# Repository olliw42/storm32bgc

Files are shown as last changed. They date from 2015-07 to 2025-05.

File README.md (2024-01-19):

STorM32 BGC
===========

<strong>STM32 32-bit microcontroller based 3-axis brushless gimbal controller board</strong>

scheme and design by OlliW (except of STorM32 v4.1)<br>
v0.17: layout by Martinez and OlliW<br>
v4.1: design by KrattWorks

latest board version: v3.3, v4.1

the STorM32 BGC boards and all other hardware published here are open source hardware, under the terms of the TAPR Open Hardware License as published by the Free Hardware Foundation, see http://www.tapr.org/ohl.html

the firmwares are free and the GUI is open source, for the details of the terms of usage/licenses see <a href="http://www.olliw.eu/2013/storm32bgc">here</a>

<strong>further resources:</strong><br>- project web page http://www.olliw.eu/2013/storm32bgc/<br>- thread at rcgroups http://www.rcgroups.com/forums/showthread.php?t=2055844<br>- wiki for the documentation http://www.olliw.eu/storm32bgc-wiki/

## v4.1 Board

Board specifically made for NT and TSTorM32 setups, with on-board motor drivers.

## v3.3 Boards

Boards specifically made for NT and TSTorM32 setups.

### STorM32 v3.3m/i

General purpose version.

### STorM32 Raspberry Pi Hat

Hat for the Raspberry Pi.

### STorM32 Micro Series

Series of stackable boards with 20x20 mm hole pattern: Main board, NT Motor-Encoder module, NT Triple Motor module, NT Logger module. 

<strong>changes in v3.3:</strong><br>- board specifically designed for NT and T-STorM32<br>- no motor drivers on board<br>- 3 NT plugs to make it easy to connect several NT modules<br>- NT-X plug carrying also the battery voltage<br>- 5 V power rail on the NT bus, with sufficient "juice"<br>- Rx&Tx on NT bus swapped, to avoid cable crossing to connect with NT modules<br>- support of stacking with a "high-power" extension board<br>- MPU9250 on board, spi (no i2c anymore!)<br>- firmware update procedure via USB<br>- ESP8266 port for WIFI connectability<br>- CAN bus port<br>- no BOOT0 button, smaller RESET button<br>- 0402 size parts<br>- board size as small as I could get it with a 2 layer design: 40 x 25 mm<br>- mounting holes, 3 mm diameter, 35 mm apart

## v1.x Boards

<strong>changes in v1.3:</strong><br>- voltage regulator in DPak package<br>- AUX2 instead of 3.3V pin at AUX port<br>- solder jumper to disconnect bluetooth led<br>- values of resistors R12,R13,R22 changed
<br><strong>changes in v1.2:</strong><br>- minor issues of v1.1 corrected<br>- Futaba S-bus support<br>- Spektrum sattelite connector<br>- usb disconnect network modified to suite F4 processors (thanks ala42!)<br>- usb voltage protection diode added (as in v0.17)<br>- further minor changes in scheme and layout
<br><strong>changes in v1.1:</strong><br>- reverse voltage protection added<br>- layout supports TC4452 motor drivers in DFN package for increased power capabilities<br>- high-side pnp open collector output for driving an IR led added<br>- additional connector for I2C#2 port added<br>- larger solder holes and pads for battery power connection<br>- improved pin arrangement for easier use

## Pictures

<strong>pictures of the v2.4 board</strong><br>


<strong>pictures of the v1.2 board (with DFN packages) and v1.3 board (with SOIC packages):</strong><br>


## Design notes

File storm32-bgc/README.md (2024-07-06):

STorM32 Boards: v1.x Series
==============

Schemes and designs by Martinez and/or OlliW.

The STorM32 boards offered in this folder are published as open source hardware, under the terms of the TAPR Open Hardware License as published by the Free Hardware Foundation, see http://www.tapr.org/ohl.html.

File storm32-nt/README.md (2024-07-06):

STorM32 Boards NT Series and NT Modules
==============

Schemes and designs by OlliW (with exceptin of the STorM32 v4.1 board). The STorM32 v4.1 board is design by [KrattWorks](https://www.krattworks.com/), [2](https://bitbucket.org/teamkrattworks/hw_storm32_v4/src/master/release/storm32-nt-v4_1/).<br>

The STorM32 boards offered in this folder are published as open source hardware, under the terms of the TAPR Open Hardware License as published by the Free Hardware Foundation, see http://www.tapr.org/ohl.html.

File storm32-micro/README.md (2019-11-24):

STorM32 Micro Boards
====================

Schemes and designs by OlliW.<br>

The STorM32 Micro boards offered in this folder are published as open source hardware, under the terms of the TAPR Open Hardware License as published by the Free Hardware Foundation, see http://www.tapr.org/ohl.html.

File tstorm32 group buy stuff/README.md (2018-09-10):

T-STorM32 Group Buy Stuff
===========

This folder contains the files, which were used in the T-STorM32 group buy on rcgroups, initiated by geekness in February 2018 (many thx geekness, and mike_kelly). It was comprised of the items

- STorM32 board v3.32m
- NT Imu module v2.11
- NT Motor-Encoder module v2.51E

Corresponding thread at rcgroups: https://www.rcgroups.com/forums/showthread.php?3027947-T-Storm-32-prototype-group-buy

A summary of using these materials for building a T-STorM32 gimbal is found here (thx funth1ngs!): https://www.rcgroups.com/forums/showpost.php?p=40180124&postcount=1033

For the Eagle .brd files hold these relations to the original Eagle files:
* 'STorM32 NT BGC v332m sz2u.brd' is different to 'STorM32 NT BGC v330m.brd'. The main change is using SM06B-SRSS connectors instead of SM07B-SRSS connectors.
* 'STorM32 NT imu v211 mini.brd' is identical to 'STorM32 NT imu v211 mini-mpu9250.brd'.
* 'T-STorM32 motor v251E-sq (Encoder).brd' is identical to 'T STorM32 motor v251E-sq.brd'.
* 'T-STorM32 motor v251E-sq (Without Encoder).brd' is identical to 'T STorM32 motor v251E-sq.brd'.

Issues
===========

Two small issues have been found with the Eagle .brd and BOM files for the NT Motor Encoder module v2.51:
* The BOM lists the TLE5012B E3005 (TLE5012BE3005XUMA1) instead of the recommended TLE5012B E1000 encoder chip.
* The Eagle .brd file shows the values for the parts C12 and R1 in confusing locations.

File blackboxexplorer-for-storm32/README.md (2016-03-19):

Acknowledgements
================

Blackbox Explorer for STorM32 is based on thenickdude's fantastic Cleanflight Blackbox Explorer, here: https://github.com/cleanflight/blackbox-log-viewer. The license is GPLv3.

Installation
================

Follow the Manual Chrome App Install procedure: Download the zip file, and unpack it to somewhere on your computer. Open Google Chrome, click on the menu button, and choose tools -> extensions. Check the developer mode checkbox in the right top corner, hit the load unpacked extension button, and browse to the unpacked folder. This adds the app to the Chrome App Launcher.

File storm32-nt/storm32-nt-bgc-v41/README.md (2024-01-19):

STorM32 Board v4.1
==================

The STorM32 v4.1 board is design by [KrattWorks](https://www.krattworks.com/).

TeamKrattWorks' repository: https://bitbucket.org/teamkrattworks/hw_storm32_v4/src/master/release/storm32-nt-v4_1/.

This STorM32 board is published as open source hardware, under the terms of the TAPR Open Hardware License as published by the Free Hardware Foundation, see http://www.tapr.org/ohl.html.

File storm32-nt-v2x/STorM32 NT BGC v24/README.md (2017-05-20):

STorM32 BGC
===========

The STorM32 v2.4 controller board is deprecated.

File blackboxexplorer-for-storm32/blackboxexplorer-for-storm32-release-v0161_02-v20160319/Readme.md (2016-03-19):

# Cleanflight Blackbox Explorer

Main explorer interface

This tool allows you to open logs recorded by Cleanflight's Blackbox feature in your web browser. You can seek through
the log to examine graphed values at each timestep. If you have a flight video, you can load that in as well and it'll
be played behind the log. You can export the graphs as a WebM video to share with others.

## Installation

There are three methods of installation available:

### Chrome Web Store method

The easiest way to get the explorer (if you have Google Chrome) is to install it from the Chrome Web Store:

https://chrome.google.com/webstore/detail/cleanflight-blackbox-expl/cahpidddaimdojnddnahjpnefajpheep

This will add it to your computer as a Chrome App.

### Manual Chrome App install
Download the contents of this repository by clicking the "download ZIP" button on the right of this page. Unpack
the zip somewhere on your computer. In Google Chrome, open up the Extensions page, tick the "developer mode" tickbox, 
click the "load unpacked extension" button, and point it at the unpacked folder. This will add it as a Chrome App.

### Run as a webpage
Download the contents of this repository by clicking the "download ZIP" button on the right of this page. Unpack
the zip somewhere on your computer, and double click "index.html" file to open it with your web browser. 

Note that the "video export" feature is only available when opened with Google Chrome. Also, running it this way will 
limit the exported flight video to 500MB in size. Use one of the previous Chrome App install methods to unlock 
&gt;500MB video export.

## Usage
Click the "Open log file/video" button at the top right and select your logged ".TXT" file and your flight video (if 
you recorded one).

You can scroll through the log by clicking or dragging on the seek bar that appears underneath the main graph. The 
current time is represented by the vertical red bar in the center of the graph. You can also click and drag left and
right on the graph area to scrub backwards and forwards.

### Syncing your log to your flight video

The blackbox plays a short beep on the buzzer when arming, and this corresponds with the start of the logged data.
You can sync your log against your flight video by pressing the "start log here" button when you hear the beep in the
video. You can tune the alignment of the log manually by pressing the nudge left and nudge right buttons in the log
sync section, or by editing the value in the "log sync" box. Positive values move the log toward the end of the video, 
negative values move it towards the beginning.

### Customizing the graph display

Click the "Graph Setup" button on the right side of the display in order to choose which fields should be plotted on
the graph. You may, for example, want to remove the default gyro plot and add separate gyro plots for each rotation axis.
Or you may want to plot vbat against throttle to examine your battery's performance.

## Notes

This tool has not been tested on Internet Explorer, but definitely won't work on versions earlier than version 9.

Your web browser must support the video codec that your flight video uses in order to play it. Firefox doesn't support
H.264 videos on Mac, so if your video won't play, try Google Chrome instead. If it still won't play, follow the 
instructions in the next section to convert your video using Handbrake.

The best performing web browser tends to be Google Chrome, especially when trying to play your flight video at the same
time.

This tool is currently in the Beta stage, so a number of key features have yet to be implemented:

- There is no control over the amount of smoothing applied to the graph lines
- There is no way to single-step between loop iterations with the arrow keys

## Flight video won't load, or jumpy flight video upon export

Some flight video formats aren't supported by Chrome, so the viewer can't open them. You can fix this by re-encoding
your video using the free tool [Handbrake][]. Open your original video using Handbrake. In the output settings, choose
MP4 as the format, and H.264 as the video codec.

Because of [Google Bug #66631][], Chrome is unable to accurately seek within H.264 videos that use B-frames. This is
mostly fine when viewing the flight video inside Blackbox Explorer. However, if you use the "export video" feature, this
bug will cause the flight video in the background of the exported video to occasionally jump backwards in time for a
couple of frames, causing a very glitchy appearance.

To fix that issue, you need to tell Handbrake to render every frame as an intraframe, which will avoid any problematic
B-frames. Do that by adding "keyint=1" into the Additional Options box:

Handbrake settings

Hit start to begin re-encoding your video. Once it finishes, you should be able to load the new video into the Blackbox
Explorer.

[Handbrake]: https://handbrake.fr/
[Google Bug #66631]: http://code.google.com/p/chromium/issues/detail?id=66631

## License

This project is licensed under GPLv3.

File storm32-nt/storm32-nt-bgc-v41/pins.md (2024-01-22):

STorM32 Board v4.1: Pin Assignment
==================

STM32 F103RC

Mot0: PB6,PB7,PB8 -> TIM4-CH1,TIM4-CH2,TIM4-CH3<br>
Mot1: PB9,PA7,PA6 -> TIM4-CH4,TIM3-CH2,TIM3-CH1<br>
Mot2: PB0,PA1,PA0 -> TIM3-CH3,TIM2-CH2,TIM2-CH1

NT: PC10,PC11 -> UART4-Tx,UART4-Rx<br>
Uart: PC12,PD2 -> UART5-Tx,UART5-Rx<br>
Uart2: PA2,PA3 -> UART2-Tx,UART2-Rx<br>
USB/Uart1: PA9,PA10 -> UART1-Tx,UART1-Rx

LEDs: PB14,PB15<br>
LIPO: PC4 -> ADC2_IN14

RC: PB11,PB10 -> UART3-Rx,UART3-Tx<br>
RC: PC7,PC9,PC6 -> TIM8-CH2,TIM8-CH4,TIM8-CH1<br>
RC#2: PC8 -> TIM8-CH3<br>
XOR: PA8<br>
POT: PB1,PC0 -> ADC1_IN9,IN10<br>
BUT: PC5<br>
AUX: PB12,PB13<br>

SPI: PB3,PB4,PB5,PA15 -> SCK3,MISO3,MOSI3,CS

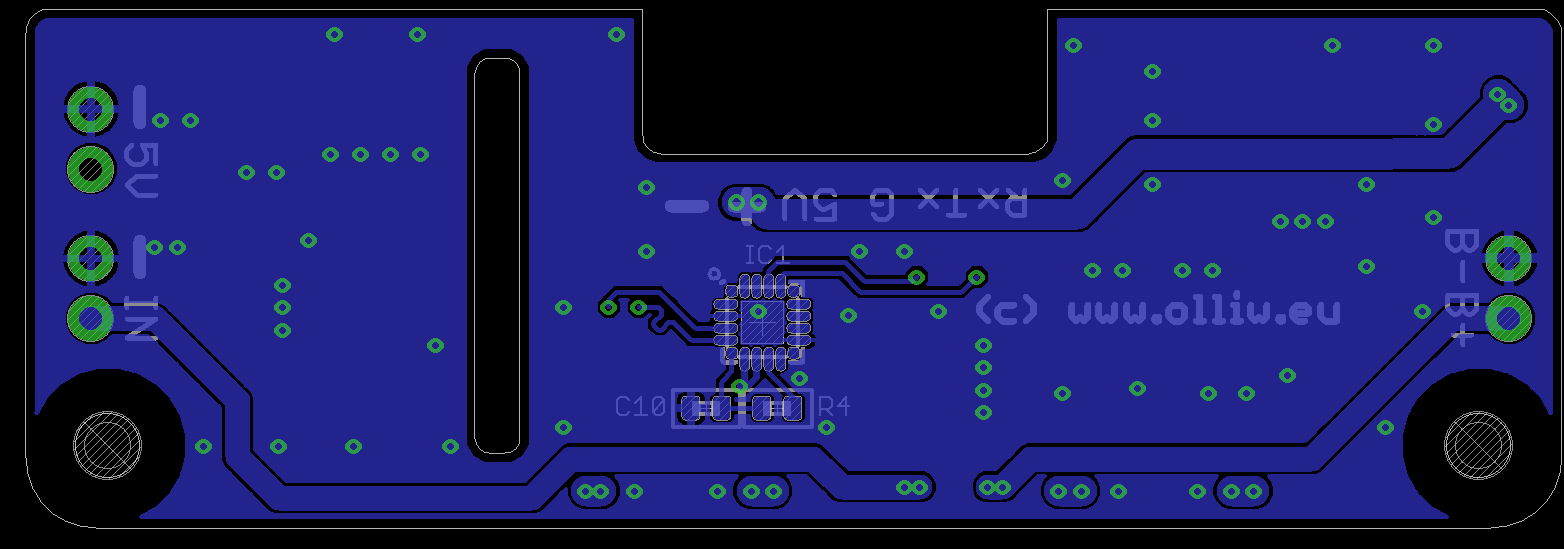
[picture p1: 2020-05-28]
storm32-rpihat/storm32-rpihat-extension-v030-bot.png

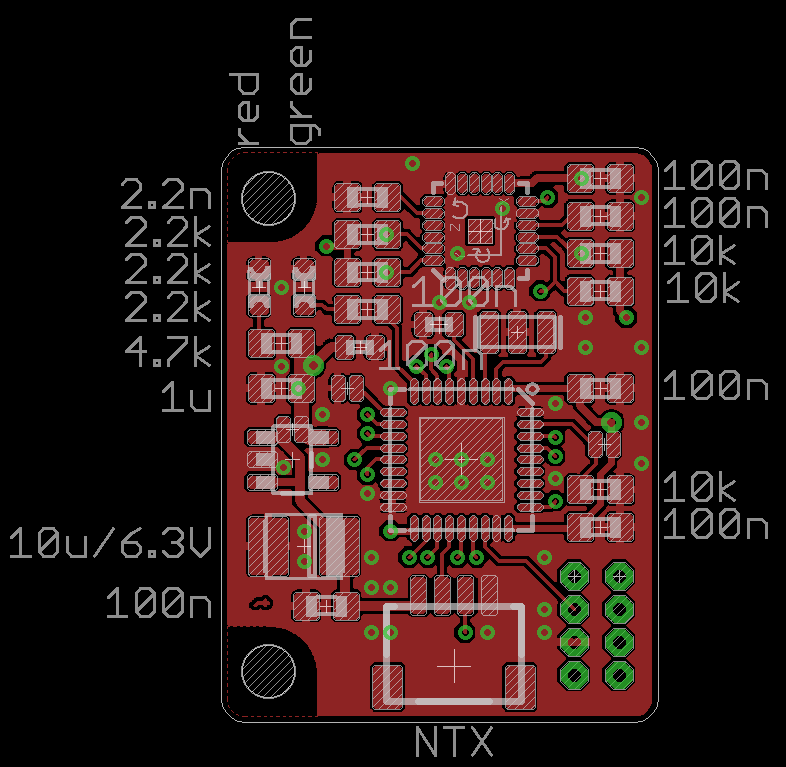
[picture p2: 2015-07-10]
storm32-nt-modules/z sub-v10/storm32-imu-module-v008-mpu6000-eagle-gerber-files-20150710/storm32-nt-imu-module-v008-mpu6000-values.png

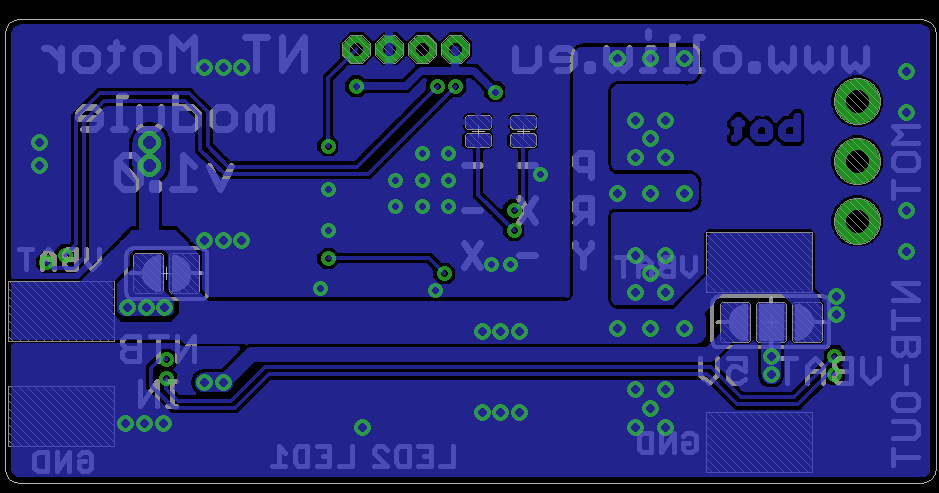
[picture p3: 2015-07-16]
storm32-nt-modules/storm32-nt-motor-modules/storm32-nt-motor-v10-bottom.png

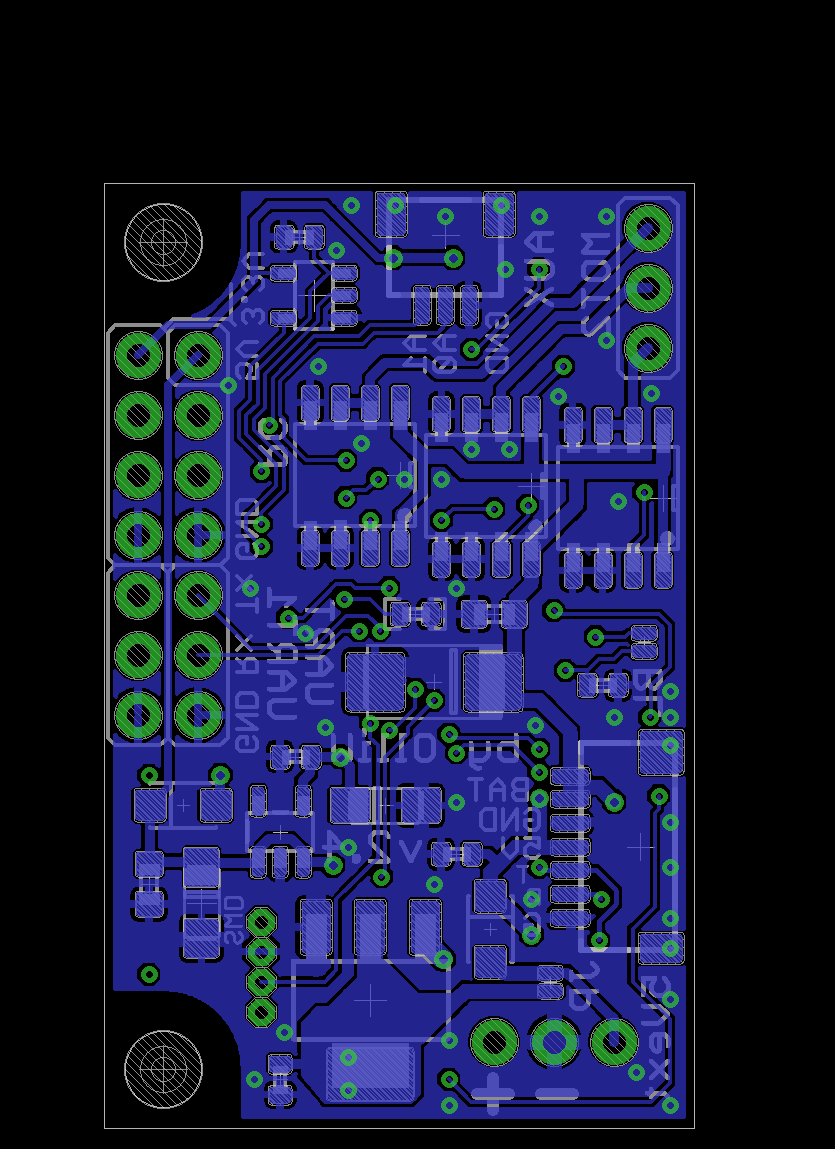
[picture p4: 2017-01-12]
storm32-nt-v2x/STorM32 NT BGC v24/storm32-nt-bgc-v24-bottom.png

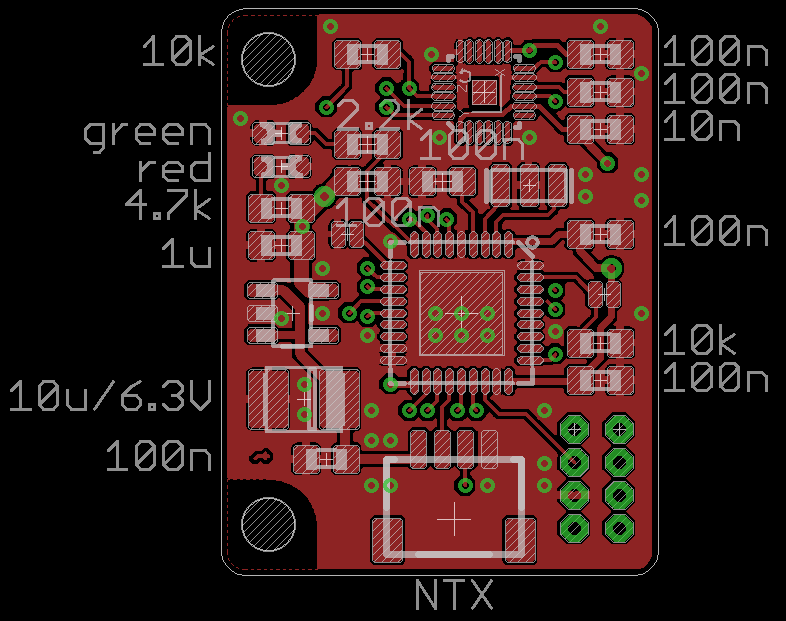
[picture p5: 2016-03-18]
storm32-nt-modules/storm32-nt-imu-modules/imu v11/storm32-nt-imu-v11-mpu9250-values.png

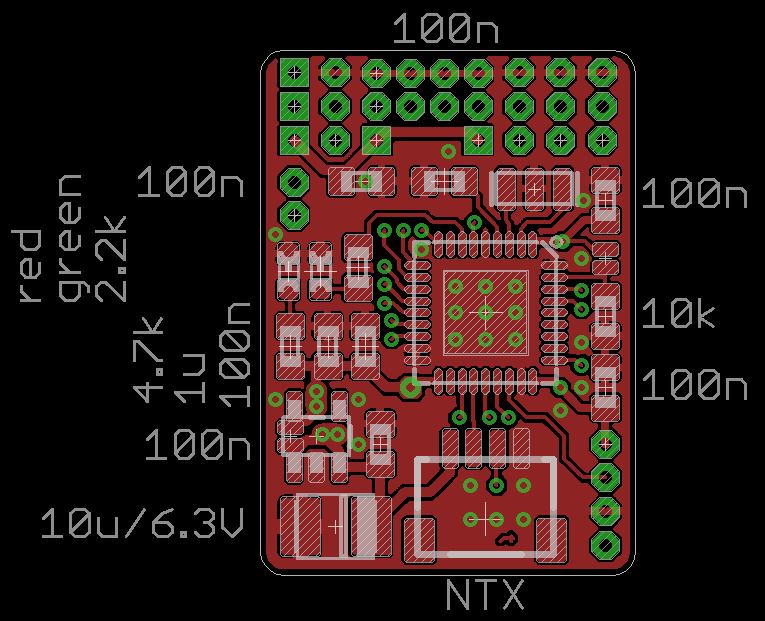
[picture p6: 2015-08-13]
storm32-nt-modules/storm32-nt-breakout/storm32-nt-breakout-v10-values.png

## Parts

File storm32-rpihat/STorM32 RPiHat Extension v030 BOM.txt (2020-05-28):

Stückliste exportiert aus C:/Users/Olli/Documents/GitHub/storm32bgc/storm32-rpihat/STorM32 RPiHat Extension v030.sch am 28.05.2020 11:59

Part  Value                    Device                 Package            Description                TP_SIGNAL_NAME
5VX   TPB1,27                  TPB1,27                B1,27              Test pad                                 
C1    4.7u/50V                 C-EUC1206              C1206              CAPACITOR, European symbol               
C2    10n                      C-EUC0603K             C0603K             CAPACITOR, European symbol               
C3    1u                       C-EUC0603K             C0603K             CAPACITOR, European symbol               
C4    100n                     C-EUC0603K             C0603K             CAPACITOR, European symbol               
C5    4.7p                     C-EUC0603K             C0603K             CAPACITOR, European symbol               
C6    47u                      C-EUC1210              C1210              CAPACITOR, European symbol               
C7    47u                      C-EUC1210              C1210              CAPACITOR, European symbol               
C8    4.7u                     C-EUC0603              C0603              CAPACITOR, European symbol               
C9    100n                     C-EUC0402              C0402              CAPACITOR, European symbol               
C10   100n                     C-EUC0402              C0402              CAPACITOR, European symbol               
C11   4.7u                     C-EUC0603              C0603              CAPACITOR, European symbol               
C12   100n                     C-EUC0402              C0402              CAPACITOR, European symbol               
C13   1u                       C-EUC0603              C0603              CAPACITOR, European symbol               
C14   100n                     C-EUC0402              C0402              CAPACITOR, European symbol               
C15   4.7u/50V                 C-EUC1206              C1206              CAPACITOR, European symbol               
C16   10n                      C-EUC0603K             C0603K             CAPACITOR, European symbol               
C17   1u                       C-EUC0603K             C0603K             CAPACITOR, European symbol               
C18   100n                     C-EUC0603K             C0603K             CAPACITOR, European symbol               
C19   4.7p                     C-EUC0603K             C0603K             CAPACITOR, European symbol               
C20   47u                      C-EUC1210              C1210              CAPACITOR, European symbol               
C21   47u                      C-EUC1210              C1210              CAPACITOR, European symbol               
IC1   CP2102N-A01-GQFN20       CP2102N-QFN20          QFN20-CP2102N                                               
IC2   NUF2042XV6               NUF2042XV6             SOT563-6                                                    
IC3   LTC4411                  LTC411SOT23-5-SPARKFUN SOT23-5-SPARKFUN                                            
IC4   LT8610A                  LT8610                 MSOP16                                                      
IC5   LTC4415                  LTC4415                LTC4415                                                     
IC6   LT8610A                  LT8610                 MSOP16                                                      
JP1                            M021X02_NO_SILK        1X02_NO_SILK       Header 2                                 
JP3                            M021X02_NO_SILK        1X02_NO_SILK       Header 2                                 
JP4                            M021X02_NO_SILK        1X02_NO_SILK       Header 2                                 
L1    ETQ-P3M2R2KVP            LL5.4X5.4              L5.4X5.4                                                    
L2    ETQ-P3M2R2KVP            LL5.4X5.4              L5.4X5.4                                                    
R1    18.2k                    R-EU_R0603             R0603              RESISTOR, European symbol                
R2    210k                     R-EU_R0603             R0603              RESISTOR, European symbol                
R3    47k                      R-EU_R0603             R0603              RESISTOR, European symbol                
R4    1k                       R-EU_R0402             R0402              RESISTOR, European symbol                
R5    18.2k                    R-EU_R0603             R0603              RESISTOR, European symbol                
R6    210k                     R-EU_R0603             R0603              RESISTOR, European symbol                
R7    47k                      R-EU_R0603             R0603              RESISTOR, European symbol                
RX-CP TPB1,27                  TPB1,27                B1,27              Test pad                                 
TX-CP TPB1,27                  TPB1,27                B1,27              Test pad                                 
U$1   SJ-2WAY-WCREAM           SJ-2WAY-WCREAM         SJ-2WAY-BIG-WCREAM                                          
U$2   SJ-2WAY-WCREAM           SJ-2WAY-WCREAM         SJ-2WAY-BIG-WCREAM                                          
USB   Amphenol 10118192-0001LF USB-MICROB             USB-MICROB         USB Connectors                           
USB1  Amphenol 10118192-0001LF USB-MICROB             USB-MICROB         USB Connectors                           
VBAT  TPB1,27                  TPB1,27                B1,27              Test pad

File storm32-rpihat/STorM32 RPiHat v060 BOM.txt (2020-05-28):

Stückliste exportiert aus C:/Users/Olli/Documents/GitHub/storm32bgc/storm32-rpihat/STorM32 RPiHat v060.sch am 28.05.2020 11:55

Part    Value                 Device                Package             Description                                                 TP_SIGNAL_NAME
3.3V1   TPB1,27               TPB1,27               B1,27               Test pad                                                                  
3.3V2   TPB1,27               TPB1,27               B1,27               Test pad                                                                  
5V      TPB1,27               TPB1,27               B1,27               Test pad                                                                  
5V1     TPB1,27               TPB1,27               B1,27               Test pad                                                                  
5VSEL   SJ-2WAY-WCREAM        SJ-2WAY-WCREAM        SJ-2WAY-BIG-WCREAM                                                                            
AUX0    TPB1,27               TPB1,27               B1,27               Test pad                                                                  
AUX1    TPB1,27               TPB1,27               B1,27               Test pad                                                                  
BL      BOOT0                 SOLDERJUMPERNO        SJ_2S-NO            Solder Jumper                                                             
BUT     TPB1,27               TPB1,27               B1,27               Test pad                                                                  
C1      10n                   C-EUC0402             C0402               CAPACITOR, European symbol                                                
C2      100n                  C-EUC0402             C0402               CAPACITOR, European symbol                                                
C3      2.2u                  C-EUC0603             C0603               CAPACITOR, European symbol                                                
C4      10u/10V               CPOL-EUSMCA           SMC_A               POLARIZED CAPACITOR, European symbol                                      
C5      100n                  C-EUC0603             C0603               CAPACITOR, European symbol                                                
C6      100n                  C-EUC0402             C0402               CAPACITOR, European symbol                                                
C7      10u/6.3V              CPOL-EUSMCA           SMC_A               POLARIZED CAPACITOR, European symbol                                      
C8      100n                  C-EUC0402             C0402               CAPACITOR, European symbol                                                
C9      100n                  C-EUC0402             C0402               CAPACITOR, European symbol                                                
C10     100n                  C-EUC0402             C0402               CAPACITOR, European symbol                                                
C11     100n                  C-EUC0402             C0402               CAPACITOR, European symbol                                                
C12     100n                  C-EUC0402             C0402               CAPACITOR, European symbol                                                
C13     100n                  C-EUC0402             C0402               CAPACITOR, European symbol                                                
C14     100n                  C-EUC0402             C0402               CAPACITOR, European symbol                                                
C15     100n                  C-EUC0402             C0402               CAPACITOR, European symbol                                                
C16     100n                  C-EUC0603             C0603               CAPACITOR, European symbol                                                
C17     100n                  C-EUC0402             C0402               CAPACITOR, European symbol                                                
C18     22p                   C-EUC0402             C0402               CAPACITOR, European symbol                                                
C19     33p                   C-EUC0402             C0402               CAPACITOR, European symbol                                                
C20     100n                  C-EUC0402             C0402               CAPACITOR, European symbol                                                
ESPGPIO TPB1,27               TPB1,27               B1,27               Test pad                                                                  
ESPRST  TPB1,27               TPB1,27               B1,27               Test pad                                                                  
IC1     STM32F103RCT6         STM32F10XRXT6         TQFP64              STM32F101/103 64pin LQFP                                                  
IC2     TC1185-3.3VCT713      V_REG_TPS76433SOT23-5 SOT23-5             Voltage Regulator                                                         
IC3     74AHC1G86             74AHC1G86             SOT23-5-VER1                                                                                  
IC4     ICM42605              ICM42605              LGA14-2.5X3                                                                                   
IC5     CAT24C32              CAT24C32              TSSOP8-4.3X3                                                                                  
IC6     SC16IS762             SC16IS762             QFN-32                                                                                        
JP1     NT-X                  SM06B-SRSS-TB         SM06B-SRSS-TB       Disconnectable Crimp style connector, 1.0mm pitch6 contacts               
JP2     NT                    SM04B-SRSS-TB         SM04B-SRSS-TB       Disconnectable Crimp style connector, 1.0mm pitch4 contacts               
JP3     JST-GH-6SIDE-ENTRY    JST-GH-6SIDE-ENTRY    SM06B-GHS-TB                                                                                  
JP4     JST-GH-6SIDE-ENTRY    JST-GH-6SIDE-ENTRY    SM06B-GHS-TB                                                                                  
LED1    green                 LEDCHIPLED_0603       CHIPLED_0603        LED                                                                       
LED2    red                   LEDCHIPLED_0603       CHIPLED_0603        LED                                                                       
LED3    orange                LEDCHIPLED_0603       CHIPLED_0603        LED                                                                       
PH1     SWD                   P4X1_1P27-OCT_BILEX   4X1_1P27_OCT_BILEX                                                                            
PH2     PINHEAD_5X1WITHOUT    PINHEAD_5X1WITHOUT    PINHEAD_5X1_WO                                                                                
PH3     RPI-UHAT              RPI-UHAT              RPI-40W-UHAT                                                                                  
PH4     PINHEAD_3X1WITHBORDER PINHEAD_3X1WITHBORDER PINHEAD_3X1                                                                                   
POT0    TPB1,27               TPB1,27               B1,27               Test pad                                                                  
POT1    TPB1,27               TPB1,27               B1,27               Test pad                                                                  
Q1      CSTCE8M00G55-R0       RESONATORSMD          RESONATOR-SMD       Resonator                                                                 
Q2      ECS-147.4-12-33-AG    QUARZ3.2X2.5          CRYSTAL-SMD-3P2X2P5                                                                           
R1      10k                   R-EU_R0402            R0402               RESISTOR, European symbol                                                 
R2      4.7k                  R-EU_R0402            R0402               RESISTOR, European symbol                                                 
R3      2.2k                  R-EU_R0402            R0402               RESISTOR, European symbol                                                 
R4      2.2k                  R-EU_R0402            R0402               RESISTOR, European symbol                                                 
R5      2.2k                  R-EU_R0402            R0402               RESISTOR, European symbol                                                 
R6      10k                   R-EU_R0402            R0402               RESISTOR, European symbol                                                 
R7      15k                   R-EU_R0402            R0402               RESISTOR, European symbol                                                 
R8      1.5k                  R-EU_R0402            R0402               RESISTOR, European symbol                                                 
R9      3.9k                  R-EU_R0402            R0402               RESISTOR, European symbol                                                 
R10     3.9k                  R-EU_R0402            R0402               RESISTOR, European symbol                                                 
R11     1k                    R-EU_R0402            R0402               RESISTOR, European symbol                                                 
R12     10k                   R-EU_R0402            R0402               RESISTOR, European symbol                                                 
R13     1k                    R-EU_R0402            R0402               RESISTOR, European symbol                                                 
R14     1k                    R-EU_R0402            R0402               RESISTOR, European symbol                                                 
RC0     TPB1,27               TPB1,27               B1,27               Test pad                                                                  
RC1     TPB1,27               TPB1,27               B1,27               Test pad                                                                  
RC2     TPB1,27               TPB1,27               B1,27               Test pad                                                                  
RX1     TPB1,27               TPB1,27               B1,27               Test pad                                                                  
RX2     TPB1,27               TPB1,27               B1,27               Test pad                                                                  
TX1     TPB1,27               TPB1,27               B1,27               Test pad                                                                  
TX2     TPB1,27               TPB1,27               B1,27               Test pad                                                                  
VBAT    TPB1,27               TPB1,27               B1,27               Test pad                                                                  
WP      SJ-2WAY-WCREAM        SJ-2WAY-WCREAM        SJ-2WAY-BIG-WCREAM

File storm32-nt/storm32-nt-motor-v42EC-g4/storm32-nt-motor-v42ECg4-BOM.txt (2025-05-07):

Stückliste exportiert aus C:/Users/Olli/Documents/GitHub/storm32bgc/storm32-nt/storm32-nt-motor-v42EC-g4/T STorM32 NT motor v42ECg4 001.sch am 07.05.2025 07:32

Part Value              Device              Package                 Description                                                 
C1   33u/20V            CPOL-EUSMCC         SMC_C                   POLARIZED CAPACITOR, European symbol                        
C2   100n               C-EUC0603           C0603                   CAPACITOR, European symbol                                  
C3   10u/10V            CPOL-EUSMCB         SMC_B                   POLARIZED CAPACITOR, European symbol                        
C4   100n               C-EUC0603           C0603                   CAPACITOR, European symbol                                  
C5   1u                 C-EUC0603           C0603                   CAPACITOR, European symbol                                  
C6   100n               C-EUC0402           C0402                   CAPACITOR, European symbol                                  
C7   100n               C-EUC0402           C0402                   CAPACITOR, European symbol                                  
C8   100n               C-EUC0402           C0402                   CAPACITOR, European symbol                                  
C9   100n               C-EUC0402           C0402                   CAPACITOR, European symbol                                  
C10  100n               C-EUC0402           C0402                   CAPACITOR, European symbol                                  
C11  100n               C-EUC0402           C0402                   CAPACITOR, European symbol                                  
C12  100n               C-EUC0402           C0402                   CAPACITOR, European symbol                                  
C13  100n               C-EUC0402           C0402                   CAPACITOR, European symbol                                  
C14  1u                 C-EUC0603           C0603                   CAPACITOR, European symbol                                  
C15  22n                C-EUC0402           C0402                   CAPACITOR, European symbol                                  
C16  22n                C-EUC0402           C0402                   CAPACITOR, European symbol                                  
C17  22n                C-EUC0402           C0402                   CAPACITOR, European symbol                                  
IC1  STM32G431KBUx      STM32G4X1KX         UFQFPN32                                                                            
IC2  LDO-TLV767         LDO-TLV767          WSON-6-2X2                                                                          
IC3  TLE5012B E1000X    TLE5012B            SO08                                                                                
IC9  DRV8311            DRV8311             QFN(WQFN)24-3X3-DRV8311                                                             
JP1  SWD                P4X1_1P27-OCT_BILEX 4X1_1P27_OCT_BILEX                                                                  
JP2  NTX-1              SM06B-SRSS-TB       SM06B-SRSS-TB           Disconnectable Crimp style connector, 1.0mm pitch6 contacts 
LED1 red                LEDCHIPLED_0603     CHIPLED_0603            LED                                                         
LED2 green              LEDCHIPLED_0603     CHIPLED_0603            LED                                                         
PH1  MOT                M031X03_NO_SILK     1X03_NO_SILK            Header 3                                                    
Q1   CSTNE8M00GH5C000R0 RESONATORSMD        RESONATOR-SMD           Resonator                                                   
R1   10k                R-EU_R0402          R0402                   RESISTOR, European symbol                                   
R2   4.7k               R-EU_R0402          R0402                   RESISTOR, European symbol                                   
R3   2.2k               R-EU_R0402          R0402                   RESISTOR, European symbol                                   
R4   1k                 R-EU_R0402          R0402                   RESISTOR, European symbol                                   
R5   330                R-EU_R0402          R0402                   RESISTOR, European symbol                                   
R6   330                R-EU_R0402          R0402                   RESISTOR, European symbol                                   
R7   330                R-EU_R0402          R0402                   RESISTOR, European symbol                                   
SJ1  BOOT0              SOLDERJUMPERNO      SJ_2S-NO                Solder Jumper                                               
SJ2  ID1                SOLDERJUMPERNO      SJ_2S-NO                Solder Jumper                                               
SJ3  ID2                SOLDERJUMPERNO      SJ_2S-NO                Solder Jumper

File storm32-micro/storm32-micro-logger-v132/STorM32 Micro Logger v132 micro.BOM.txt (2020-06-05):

Stückliste exportiert aus C:/Users/Olli/Documents/GitHub/storm32bgc/storm32-micro/storm32-micro-logger-v132/STorM32 Micro Logger v132 micro.sch am 05.06.2020 16:31

Part Value              Device                Package            Description                                                 
C1   10u/10V            CPOL-EUSMCB           SMC_B              POLARIZED CAPACITOR, European symbol                        
C2   100n               C-EUC0603             C0603              CAPACITOR, European symbol                                  
C3   1u                 C-EUC0603             C0603              CAPACITOR, European symbol                                  
C4   100n               C-EUC0402             C0402              CAPACITOR, European symbol                                  
C5   100n               C-EUC0402             C0402              CAPACITOR, European symbol                                  
C6   100n               C-EUC0402             C0402              CAPACITOR, European symbol                                  
C7   100n               C-EUC0402             C0402              CAPACITOR, European symbol                                  
C8   100n               C-EUC0402             C0402              CAPACITOR, European symbol                                  
C9   100n               C-EUC0603             C0603              CAPACITOR, European symbol                                  
C10  100n               C-EUC0402             C0402              CAPACITOR, European symbol                                  
IC1  STM32F103T8        STM32F10XTXU6         VFQFPN36           STM32F101/103 36pad VFQPFN36                                
IC2  TC1015-3.3VCT713   V_REG_TPS76433SOT23-5 SOT23-5            Voltage Regulator                                           
IC3  DS3231M            DS3231M               SO08                                                                           
JP1  PINHEAD_5X1WITHOUT PINHEAD_5X1WITHOUT    PINHEAD_5X1_WO                                                                 
LED1 red                LEDCHIPLED_0603       CHIPLED_0603       LED                                                         
LED2 green              LEDCHIPLED_0603       CHIPLED_0603       LED                                                         
NTX  NTX                SM04B-SRSS-TB         SM04B-SRSS-TB      Disconnectable Crimp style connector, 1.0mm pitch4 contacts 
PH1  SWD                P4X1_1P27-OCT_BILEX   4X1_1P27_OCT_BILEX                                                             
Q1   CSTCE8M00G55-R0    RESONATORSMD          RESONATOR-SMD      Resonator                                                   
R1   4.7k               R-EU_R0402            R0402              RESISTOR, European symbol                                   
R2   2.2k               R-EU_R0402            R0402              RESISTOR, European symbol                                   
R3   47k                R-EU_R0402            R0402              RESISTOR, European symbol                                   
R4   47k                R-EU_R0402            R0402              RESISTOR, European symbol                                   
R5   1k                 R-EU_R0402            R0402              RESISTOR, European symbol                                   
R6   1k                 R-EU_R0402            R0402              RESISTOR, European symbol                                   
U$1  CELLCLIP10MM       CELLCLIP10MM          CELLCLIP-10MM                                                                  
U1   3M 2908-05WB-MG ?? MICROSD               MICROSD            Micro-SD / Transflash card holder with SPI pinout

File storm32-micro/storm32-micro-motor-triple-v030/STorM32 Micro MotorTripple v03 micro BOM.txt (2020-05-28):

Stückliste exportiert aus C:/Users/Olli/Documents/GitHub/storm32bgc/storm32-micro/storm32-micro-motor-triple-v030/STorM32 Micro MotorTripple v03 micro.sch am 28.05.2020 12:03

Part Value              Device                Package            Description                                                 
C1   33u/20V            CPOL-EUSMCB           SMC_B              POLARIZED CAPACITOR, European symbol                        
C2   100n               C-EUC0603             C0603              CAPACITOR, European symbol                                  
C3   10u/10V            CPOL-EUSMCA           SMC_A              POLARIZED CAPACITOR, European symbol                        
C4   100n               C-EUC0402             C0402              CAPACITOR, European symbol                                  
C5   1u                 C-EUC0603             C0603              CAPACITOR, European symbol                                  
C6   100n               C-EUC0402             C0402              CAPACITOR, European symbol                                  
C7   100n               C-EUC0402             C0402              CAPACITOR, European symbol                                  
C8   100n               C-EUC0402             C0402              CAPACITOR, European symbol                                  
C9   100n               C-EUC0402             C0402              CAPACITOR, European symbol                                  
C10  100n               C-EUC0603             C0603              CAPACITOR, European symbol                                  
C11  100n               C-EUC0603             C0603              CAPACITOR, European symbol                                  
C12  100n               C-EUC0603             C0603              CAPACITOR, European symbol                                  
IC1  STM32F10XTXU6      STM32F10XTXU6         VFQFPN36           STM32F101/103 36pad VFQPFN36                                
IC2                     V_REG_TPS76433SOT23-5 SOT23-5            Voltage Regulator                                           
IC3  DRV8839            DRV8839               WSON-12-2X3MM                                                                  
IC4  DRV8839            DRV8839               WSON-12-2X3MM                                                                  
IC5  DRV8839            DRV8839               WSON-12-2X3MM                                                                  
IC6  DRV8839            DRV8839               WSON-12-2X3MM                                                                  
IC7  DRV8839            DRV8839               WSON-12-2X3MM                                                                  
JP1  NTX-1              SM06B-SRSS-TB         SM06B-SRSS-TB      Disconnectable Crimp style connector, 1.0mm pitch6 contacts 
JP3  SWD                P4X1_1P27-OCT_BILEX   4X1_1P27_OCT_BILEX                                                             
JP4  MOT                M03PTH                1X03               Header 3                                                    
JP5  MOT                M03PTH                1X03               Header 3                                                    
JP6  MOT                M03PTH                1X03               Header 3                                                    
LED1 red                LEDCHIPLED_0603       CHIPLED_0603       LED                                                         
LED2 green              LEDCHIPLED_0603       CHIPLED_0603       LED                                                         
Q1   RESONATORSMD       RESONATORSMD          RESONATOR-SMD      Resonator                                                   
R1   10k                R-EU_R0402            R0402              RESISTOR, European symbol                                   
R2   4.7k               R-EU_R0402            R0402              RESISTOR, European symbol                                   
R3   2.2k               R-EU_R0402            R0402              RESISTOR, European symbol                                   
SJ1  BOOT0              SOLDERJUMPERNO        SJ_2S-NO           Solder Jumper                                               
U$1  PINHEAD_5X1WITHOUT PINHEAD_5X1WITHOUT    PINHEAD_5X1_WO

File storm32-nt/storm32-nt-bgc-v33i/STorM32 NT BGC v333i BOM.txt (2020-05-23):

Stückliste exportiert aus C:/Users/Olli/Documents/GitHub/storm32bgc/storm32-nt/storm32-nt-bgc-v33i/STorM32 NT BGC v333i.sch am 23.05.2020 11:32

Part  Value                    Device                  Package                         Description                                                 
BAT+                           M1X1                    1X1_WITHOUT                                                                                 
BAT-                           M1X1                    1X1_WITHOUT                                                                                 
BL    BOOT0                    SOLDERJUMPERNO          SJ_2S-NO                        Solder Jumper                                               
C1    10u/35V                  CPOL-EUSMCB             SMC_B                           POLARIZED CAPACITOR, European symbol                        
C2    1u/25V                   C-EUC0603               C0603                           CAPACITOR, European symbol                                  
C3    1u                       C-EUC0603               C0603                           CAPACITOR, European symbol                                  
C4    10u/10V                  CPOL-EUSMCA             SMC_A                           POLARIZED CAPACITOR, European symbol                        
C5    100n                     C-EUC0603               C0603                           CAPACITOR, European symbol                                  
C6    100n                     C-EUC0402               C0402                           CAPACITOR, European symbol                                  
C7    10u/6.3V                 CPOL-EUSMCA             SMC_A                           POLARIZED CAPACITOR, European symbol                        
C8    100n                     C-EUC0402               C0402                           CAPACITOR, European symbol                                  
C9    100n                     C-EUC0402               C0402                           CAPACITOR, European symbol                                  
C10   100n                     C-EUC0402               C0402                           CAPACITOR, European symbol                                  
C11   100n                     C-EUC0402               C0402                           CAPACITOR, European symbol                                  
C12   100n                     C-EUC0402               C0402                           CAPACITOR, European symbol                                  
C13   100n                     C-EUC0402               C0402                           CAPACITOR, European symbol                                  
C14   100n                     C-EUC0402               C0402                           CAPACITOR, European symbol                                  
C15   4.7u                     C-EUC0603               C0603                           CAPACITOR, European symbol                                  
C16   2.2u                     C-EUC0603               C0603                           CAPACITOR, European symbol                                  
C17   100n                     C-EUC0402               C0402                           CAPACITOR, European symbol                                  
C18   10n                      C-EUC0402               C0402                           CAPACITOR, European symbol                                  
C19   100n                     C-EUC0402               C0402                           CAPACITOR, European symbol                                  
C20   100n                     C-EUC0402               C0402                           CAPACITOR, European symbol                                  
C21   100n                     C-EUC0402               C0402                           CAPACITOR, European symbol                                  
C22   1u                       C-EUC0603               C0603                           CAPACITOR, European symbol                                  
C23   10u/10V                  CPOL-EUSMCA             SMC_A                           POLARIZED CAPACITOR, European symbol                        
D1    PMEG3010ER               DIODE-SCHOTTKYSOD123-W  SOD123W-DIODE                                                                               
D2    PMEG3010ER               DIODE-SCHOTTKYSOD123-W  SOD123W-DIODE                                                                               
D3    PMEG3010ER               DIODE-SCHOTTKYSOD123-W  SOD123W-DIODE                                                                               
D4    PMEG3010ER               DIODE-SCHOTTKYSOD123-W  SOD123W-DIODE                                                                               
D5    BAT54J                   DIODE-SOD110-R          SOD110-R                        DIODE                                                       
D6    BAT54J                   DIODE-SOD110-R          SOD110-R                        DIODE                                                       
IC1   STM32F103RCT6            STM32F10XRXT6           TQFP64                          STM32F101/103 64pin LQFP                                    
IC2   TC1185-3.3VCT713         V_REG_TPS76433SOT23-5   SOT23-5                         Voltage Regulator                                           
IC3   LMR14206                 MP2359                  SOT23-6                                                                                     
IC4   CP2102N-A01-GQFN20       CP2102N-QFN20           QFN20-CP2102N                                                                               
IC5   74AHC1G86                74AHC1G86               SOT23-5-VER1                                                                                
IC6   ICM42605                 ICM42605                LGA14-2.5X3                                                                                 
IC7   TJA1051TK/3              TJA1051TK/3             HVSON8                                                                                      
JP1   SWD                      P4X1_1P27-OCT_BILEX     4X1_1P27_OCT_BILEX                                                                          
JP2   RC                       M041X04_NO_SILK         1X04_NO_SILK                    Header 4                                                    
JP3   RC2                      M041X04_NO_SILK         1X04_NO_SILK                    Header 4                                                    
JP4   UART1                    M031X03_NO_SILK         1X03_NO_SILK                    Header 3                                                    
JP5   UART#2                   M031X03_NO_SILK         1X03_NO_SILK                    Header 3                                                    
JP6   RC2                      M041X04_NO_SILK         1X04_NO_SILK                    Header 4                                                    
JP7   POT/BUT                  SM05B-SRSS-TB           SM05B-SRSS-TB                   Disconnectable Crimp style connector, 1.0mm pitch5 contacts 
JP8   AUX                      SM03B-SRSS-TB           SM03B-SRSS-TB                   Disconnectable Crimp style connector, 1.0mm pitch3 contacts 
JP9   NT-X                     SM06B-SRSS-TB           SM06B-SRSS-TB                   Disconnectable Crimp style connector, 1.0mm pitch6 contacts 
JP10  NT                       SM04B-SRSS-TB           SM04B-SRSS-TB                   Disconnectable Crimp style connector, 1.0mm pitch4 contacts 
JP11  NT                       SM04B-SRSS-TB           SM04B-SRSS-TB                   Disconnectable Crimp style connector, 1.0mm pitch4 contacts 
JP12  UART2                    M031X03_NO_SILK         1X03_NO_SILK                    Header 3                                                    
JP13  ESP                      M031X03_NO_SILK         1X03_NO_SILK                    Header 3                                                    
L1    LPS4018-103MRC           L                       L4X4                                                                                        
LED1  green                    LEDCHIPLED_0603         CHIPLED_0603                    LED                                                         
LED2  red                      LEDCHIPLED_0603         CHIPLED_0603                    LED                                                         
Q1    CSTCE8M00G55-R0          RESONATORSMD            RESONATOR-SMD                   Resonator                                                   
R1    10k                      R-EU_R0402              R0402                           RESISTOR, European symbol                                   
R4    1k                       R-EU_R0402              R0402                           RESISTOR, European symbol                                   
R5    10k                      R-EU_R0402              R0402                           RESISTOR, European symbol                                   
R6    1k                       R-EU_R0402              R0402                           RESISTOR, European symbol                                   
R7    5.62k                    R-EU_R0402              R0402                           RESISTOR, European symbol                                   
R8    15k                      R-EU_R0402              R0402                           RESISTOR, European symbol                                   
R9    1.5k                     R-EU_R0402              R0402                           RESISTOR, European symbol                                   
R10   2.2k                     R-EU_R0402              R0402                           RESISTOR, European symbol                                   
R11   2.2k                     R-EU_R0402              R0402                           RESISTOR, European symbol                                   
R12   2.2k                     R-EU_R0402              R0402                           RESISTOR, European symbol                                   
R13   4.7k                     R-EU_R0402              R0402                           RESISTOR, European symbol                                   
R14   10k                      R-EU_R0402              R0402                           RESISTOR, European symbol                                   
R15   10k                      R-EU_R0402              R0402                           RESISTOR, European symbol                                   
R16   10k                      R-EU_R0402              R0402                           RESISTOR, European symbol                                   
RESET TL1014AF160QG            SWITCH-SMD-RIGHT-TL1014 TACTILE-SWITCH-SMD-RIGHT-TL1014                                                             
USB   Amphenol 10118192-0001LF USB-MICROB              USB-MICROB                      USB Connectors

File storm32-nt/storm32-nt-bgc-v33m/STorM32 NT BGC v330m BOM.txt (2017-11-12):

Stückliste exportiert aus C:/Users/Olli/Documents/GitHub/storm32bgc/storm32-nt/storm32-nt-bgc-v330m/STorM32 NT BGC v330m.sch am 12.11.2017 04:34

Part  Value                    Device                  Package                         Description                                                 
BAT+                           M1X1                    1X1_WITHOUT                                                                                 
BAT-                           M1X1                    1X1_WITHOUT                                                                                 
BL    BOOT0                    SOLDERJUMPERNO          SJ_2S-NO                        Solder Jumper                                               
C1    10u/20V                  CPOL-EUSMCB             SMC_B                           POLARIZED CAPACITOR, European symbol                        
C2    1u                       C-EUC0603               C0603                           CAPACITOR, European symbol                                  
C3    1u                       C-EUC0603               C0603                           CAPACITOR, European symbol                                  
C4    10u/10V                  CPOL-EUSMCA             SMC_A                           POLARIZED CAPACITOR, European symbol                        
C5    100n                     C-EUC0603               C0603                           CAPACITOR, European symbol                                  
C6    100n                     C-EUC0402               C0402                           CAPACITOR, European symbol                                  
C7    10u/6.3V                 CPOL-EUSMCA             SMC_A                           POLARIZED CAPACITOR, European symbol                        
C8    100n                     C-EUC0402               C0402                           CAPACITOR, European symbol                                  
C9    100n                     C-EUC0402               C0402                           CAPACITOR, European symbol                                  
C10   100n                     C-EUC0402               C0402                           CAPACITOR, European symbol                                  
C11   100n                     C-EUC0402               C0402                           CAPACITOR, European symbol                                  
C12   100n                     C-EUC0402               C0402                           CAPACITOR, European symbol                                  
C13   100n                     C-EUC0402               C0402                           CAPACITOR, European symbol                                  
C14   100n                     C-EUC0402               C0402                           CAPACITOR, European symbol                                  
C15   4.7u                     C-EUC0603               C0603                           CAPACITOR, European symbol                                  
C16   100n                     C-EUC0402               C0402                           CAPACITOR, European symbol                                  
C17   10n                      C-EUC0402               C0402                           CAPACITOR, European symbol                                  
C18   100n                     C-EUC0402               C0402                           CAPACITOR, European symbol                                  
C19   100n                     C-EUC0402               C0402                           CAPACITOR, European symbol                                  
C20   100n                     C-EUC0402               C0402                           CAPACITOR, European symbol                                  
C21   100n                     C-EUC0402               C0402                           CAPACITOR, European symbol                                  
C22   1u                       C-EUC0603               C0603                           CAPACITOR, European symbol                                  
C23   10u/10V                  CPOL-EUSMCA             SMC_A                           POLARIZED CAPACITOR, European symbol                        
D1    PMEG3010ER               DIODE-SCHOTTKYSOD123-W  SOD123W-DIODE                                                                               
D2    PMEG3010ER               DIODE-SCHOTTKYSOD123-W  SOD123W-DIODE                                                                               
D3    PMEG3010ER               DIODE-SCHOTTKYSOD123-W  SOD123W-DIODE                                                                               
D4    PMEG3010ER               DIODE-SCHOTTKYSOD123-W  SOD123W-DIODE                                                                               
D5    1PS76SB40                DIODE-SOD110-R          SOD110-R                        DIODE                                                       
D6    1PS76SB40                DIODE-SOD110-R          SOD110-R                        DIODE                                                       
IC1   STM32F103RCT6            STM32F10XRXT6           TQFP64                          STM32F101/103 64pin LQFP                                    
IC2   MPU9250                  IMU3000QFN-24-0.4MIL    QFN-24-3X3                                                                                  
IC3   LMR14206                 MP2359                  SOT23-6                                                                                     
IC4   TC1185-3.3VCT713         V_REG_TPS76433SOT23-5   SOT23-5                         Voltage Regulator                                           
IC5   CP2102N-QFN20            CP2102N-QFN20           QFN20-CP2102N                                                                               
IC6   TJA1051TK/3              TJA1051TK/3             HVSON8                                                                                      
IC7   74AHC1G86                74AHC1G86               SOT23-5-VER1                                                                                
JP1   SWD                      P4X1_1P27-OCT_BILEX     4X1_1P27_OCT_BILEX                                                                          
JP2   RC                       M041X04_NO_SILK         1X04_NO_SILK                    Header 4                                                    
JP3   RC2                      M041X04_NO_SILK         1X04_NO_SILK                    Header 4                                                    
JP4   UART1                    M031X03_NO_SILK         1X03_NO_SILK                    Header 3                                                    
JP5   UART#2                   M031X03_NO_SILK         1X03_NO_SILK                    Header 3                                                    
JP6   RC2                      M041X04_NO_SILK         1X04_NO_SILK                    Header 4                                                    
JP7   POT/BUT                  SM05B-SRSS-TB           SM05B-SRSS-TB                   Disconnectable Crimp style connector, 1.0mm pitch5 contacts 
JP8   AUX                      SM03B-SRSS-TB           SM03B-SRSS-TB                   Disconnectable Crimp style connector, 1.0mm pitch3 contacts
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

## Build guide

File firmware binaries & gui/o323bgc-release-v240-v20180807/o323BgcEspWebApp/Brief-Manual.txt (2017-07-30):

brief instructions for using the ESP8266 wifi support

0) you need a black ESP-01 (i.e. a ESP-01 with 1M instead of 0.5M)(typically they come with a label "AI-Cloud inside", or as ESP-01s "s series").

1) you need to flash the firmware onto the ESP
- connect the ESP to a usb-ttl adapter and connect the pins to bring it into bootloader mode, exactly as explained on one of the many instructions on the web
- browse to the o323BgcEspWebApp directory in the STorM32 firmware folder
- double click cmd-here.bat
- enter uploadInoBin COM??, where COM?? stands for the com port (e.g. COM23), and hit enter

2) you need to upload the files in the data subfolder to the SPIFFS file system
- connect the ESP to a usb-ttl adapter and connect the pins to bring it into bootloader mode, exactly as explained on one of the many instructions on the web
- browse to the o323BgcEspWebApp directory in the StorM32 firmware folder
- double click cmd-here.bat
- enter uploadDataToFs COM??, where COM?? stands for the com port (e.g. COM23), and hit enter

3) Connect the ESP to the STorM32 board
- connect the ESP's Tx and Rx pins to the STorM32's UART Rx and Tx pins
- provide 3.3V power to the ESP (do NOT use the STorM32's 3.3V pins, they are too weak)(do NOT use voltages larger than 3.3V)

4) Configure ESP in STorM32 GUI
- set the parameter "Esp Configuration" in the Expert tab to "Uart"

5) Connect Wifi 
By default the ESP is configured as access point with ssid "STorM32 ESP" and password "thisisgreat". So, connect to it, start the browser, and go to 192.168.4.1. Alternative, start the GUI and choose "ESP" in teh Port field.

You are greatly encouraged to improve the javascript and css files. This is made very easy. The ESP just provides a very rudimentary HTML skeleton, everything essential is filled in by the js and css scripst, and these are stored in the ESP's filesystem. In order to use your own js and css, you just have to upload them to the EPS's filesystem (step 3). You also can provide links to js and css files on your own webspace, which makes development most easy. See storm32web.cfg for details.

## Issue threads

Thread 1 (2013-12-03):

STorM32 BGC board v0.17

olliw42, 2013-12-03:
this board doesn't (yet) have a reverse battery protection
please be very carefull and DO NOT CONNECT THE BATTERY WITH INCORRECT POLARITY!
this would destroy many of the TC4452 drivers, and maybe other parts too

the solder pads for the tactile switches are small, and mechanically fragile
please glue the two switches to the print board!

I have build and tested now several boards, besides the two issues above the board works exactly as expected :)

olliw42, 2020-01-08:
board is deprecated

Closed 2020-01-08.

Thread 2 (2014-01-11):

STorM32 BGC board v1.10

olliw42, 2014-01-11:
This board does work perfectly, it hasn't any electrical issues.

However, it has some minor mistakes/imperfections:
- the labelling of the SWD port is incorrect, it should be SWDIO,GND,SWCLK,3.3V (instead of GND,SWCLK,SWDIO,3.3V)
- the two big solder holes for the battery cable are missing solder rings on the bottom
- the sequence of pins of the I2C#2 port is reverse as compared to that of the MPU I2C port (hence, and IMU module connected the MPU port MUST NOT be connecetd to the I2C#2 port, and vice versa)

Obviously, these points will be taken care in the next release.

CradyCopter, 2015-02-15:
Hi Olli,

I have a new v1.1 board that arrived without firmware installed from Witespy.

I was able to successfully flash the firmware several times but after every flashing I Windows 7 never assigns a COM port to the board and the GUI can't see it.

Tried several re-flashes, power cycling, different cables, etc. but regardless of which USB port I try on my computer Windows never sees board.

olliw42, 2020-01-08:
board is deprecated

Closed 2020-01-08.

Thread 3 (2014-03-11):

STorM32 BGC board v1.2 rev1

olliw42, 2014-03-11:
minor issue: no cream for the central pad of the DFN packages, this affects stencils

olliw42, 2020-01-08:
board is deprecated

Closed 2020-01-08.

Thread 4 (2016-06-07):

Can't connect to gimbal - "Read...Aborted!"

chicco4life, 2016-06-07:
Hi,

I just purchased a GoodluckBuy gimbal with the v1.31 Storm32 board.  I have installed the driver for my ttl-usb converter and plugged it in.  I was able to open up the V0.8 GUI and flash its firmware - yet after firmware flashing is successful, I can't seem to boot up the gimbal from my computer.  It says Read...Aborted, and asks me to read first.  Yet when I press read, it gives me the same error message.  Could you please help?

olliw42, 2020-01-08:
outdated

Closed 2020-01-08.

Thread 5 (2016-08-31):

Storm32NT 2.11e IMU orientation switched

Gregmaan, 2016-08-31:
Hi,
with 2 NT IMUs connected (Ensys NT V2.0) the measurements of the "Configure Gibal tool" IMU orientation are switched:

Orientation of IMU1 is IMU2 and IMU2 is IMU1.

olliw42, 2020-01-08:
outdated

Closed 2020-01-08.

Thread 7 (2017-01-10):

MOST usful feature suggestion

Tommixoft, 2017-01-10:
Hi, yesterday i though of super feature to add to board - current draw info. SO people can see in "real time" how much current is drawn so by this we can know how good we balanced gimbal, If you dont have ability to add amps - you maybe can think something by using info you sending to motor controllers. SO if there is high amount of correction sent -this means bad calibration (of course if gimbal is in steady position).
I think such feature would be great.

Tommixoft, 2017-01-12:
sad this is dead project.

noradtux, 2017-01-12:
Try to contact olliw on rcgroups.com. This project is far from dead, but it's not using github as it's primary development plattform.

Tommixoft, 2017-01-12:
@noradtux RC groups is filled with noob questions and in 1 hour my suggestion would be 5 pages behind :) So i put here. What do you think about my feature? Would it be useful to you?

noradtux, 2017-01-12:
@Tommixoft I think using the NT-logger provides better means of evaluating how well the system is balanced. So no, I wouldn't consider measuring current draw to have any benefit over what is already there.

Tommixoft, 2017-01-12:
NT logger works with NON nt firmware? Cause all that nt stuff is overrated. i in my entire using never got even single I2C error.

noradtux, 2017-01-12:
Well, development of non-NT-stuff has effectively halted. NT isn't just about better rejection of interference, it also gives benefits like the nt-logger and camera modules, giving me more functionality with less wires. I could even reduce wires more if I used the motor modules.

Tommixoft, 2017-01-12:
Hmmm camera modules? what is this? Maybe i will buy NT sensor some day, my country makes them, anyways, im using this board as gimbal for camera, not on drone, so so far it provides all needed functions, but i wish firmware be open source, now everything depends on 1 person.

noradtux, 2017-01-12:
I use a cc3d atom as camera-IMU. I can use two of its servo outputs to control the camera. I think you will find the wiki enlightening.

olliw42, 2020-01-08:
the hardware can't do current measuerment
outdated

Closed 2020-01-08.

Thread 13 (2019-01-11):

When the frost, the suspension begins chaos

whakru, 2019-01-11:
When I start to use the suspension when the frost is at -5 and below (I leave the house to the street). After some time (1-5 minutes) the suspension starts to throw in different directions, chaos begins. But after rebooting everything comes back to normal. Sensor used on I2C error 0.
If the suspension is frozen for 5-10 minutes on the street, then the mayhem does not occur
....
Когда я начинаю использовать подвес при морозе в -5 и ниже (выхожу из дома на улицу). То через какое то время (1-5 минут) подвес начинает кидать в разные стороны, начинается беспредел. Но после перезагрузки все приходит в норму. Используется датчик на I2C ошибок 0.
Если подвес проморозить минут 5-10 на улице то беспредела  не просиходит

olliw42, 2020-01-08:
shouldn't happen really
try leaving the gimbal outside for some 10 minutes and 5then restart
outdated

Closed 2020-01-08.

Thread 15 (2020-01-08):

IMU not available

Vishranthee, 2020-01-08:
I tried my level best and went through all the RC group pages and re-flashed the firmware multiple times. But IMU is not available and I'm unable to calibrate it by any means.

Power LED is solid.  @olliw42

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

olliw42, 2020-01-08:
you probably have a I2C-based IMU and not an NT IMU, ie., use the wrong firmware. Please read up in the wiki: http://www.olliw.eu/storm32bgc-wiki/Downloads

the primary location for questions & discussions is btw here: https://www.rcgroups.com/forums/showthread.php?2055844-STorM32-BGC-32-bit-3-axis-brushless-gimbal-controller

olliw42, 2020-03-26:
no further response so seems to be resolved and I close :)

Closed 2020-03-26.

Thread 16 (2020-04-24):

Question: Can you use the storm 32 as a driver

finnBsch, 2020-04-24:
Hi,
I am desperately looking for a way to drive gimbal motors with an arduino.  I don't use the gimbal motors in a gimbal, so the storm32 board isn't helping.  However since it has the capability to drive these motors, maybe there's a way to use it to speed controll the motors based on arduino input? No stabilization whatsoever is  needed though..

olliw42, 2020-05-23:
I can do that using what it calls the "servo" mode

by principle, without encoders, the rotation is however not very "smooth" (issue is motor cogging)

I think this answers this, so I'm closing. If you have more questions on this, please reopen, or even better, join the rcgroups discussion thread :)

Closed 2020-05-23.

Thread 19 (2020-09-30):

10 magnets on motor at 0.90 i2c

whoim2, 2020-09-30:
Hello! Have motors with 10 magnets, but in program 0.90 may set minimum 12. Motor work, but have hissing sound in many positions.
What im may set 10 magnets?
drv8313, pcb diy as 1.31
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

whoim2, 2020-10-01:
im try to set 10 poles via set command in "rc input", command 20, 26, 32. Value 10, and store to eeprom. Read button and log write: 10 poles. But strange hissing sound present.

olliw42, 2020-10-03:
use a latest firmware, it supports 10 poles
it needs to be however a NT setup, and not I2C

whoim2, 2020-10-03:
> use a latest firmware, it supports 10 poles
> it needs to be however a NT setup, and not I2C

Not have nt imu module (
 0.96 fw not support 10 poles, if im set value from setcommand?
Ok, i understand. Thanks.

olliw42, 2020-10-03:
I think the approach you've tried should have worked, not sure why it didn't
maybe you best bet is to patch the GUI exe. It's perl, and Perl is an interpreter, so in the exe you just find the source packed with the interpreter. Hence, it could be possible to just patsh the limits for the motor poles.
Have fun.

whoim2, 2020-10-03:
> I think the approach you've tried should have worked, not sure why it didn't
> maybe you best bet is to patch the GUI exe. It's perl, and Perl is an interpreter, so in the exe you just find the source packed with the interpreter. Hence, it could be possible to just patsh the limits for the motor poles.
> Have fun.

Maybe, hissing sound not because of the poles?
Im try today verify poles at log and tests

whoim2, 2020-10-03:
> I think the approach you've tried should have worked, not sure why it didn't
> maybe you best bet is to patch the GUI exe. It's perl, and Perl is an interpreter, so in the exe you just find the source packed with the interpreter. Hence, it could be possible to just patsh the limits for the motor poles.
> Have fun.

You may say about compile software for perl? pl file found at 0.96 folder. Latest active perl for win?
Have win7 and ubuntu

Closed 2020-10-03.

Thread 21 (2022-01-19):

I have error NT Imu.

muharremcaglayan, 2022-01-19:
Hi I have Storm32 BGC v1.32 and I'm using 2.59e version also I have Nt IMU v2.1 with 9250  I tried many firmware in pitcure 2.53e, I dont make any calibration because no any change accel y data. It's not working, what should I do every thing is OK. ?

accel calibration pitcure
https://www.hizliresim.com/nl96bio

IMU status is ok .
https://www.hizliresim.com/gbmvgtn

Closed 2022-12-31.

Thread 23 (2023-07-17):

Question: how one could reach the most responsive control and highest rotation speeds?

alpha358, 2023-07-17:
Hello I have two maybe uneducated questions,
**1) Are there rotation speed limitations hard-coded inside a firmware?**

I turn off the speed and acceleration limitations of the STorM32 gimbal by using o323BGCTool.
The gimbal rotates faster, but still it is much slower when compared to what the powerful BLDC engines can provide - I see much faster rotations when I turn the gimbal to a different position with my hand then it is commanded to be in, then after I release it - it is returning to the original position much, much faster then what I get when I simply send MAVLINK rotation commands to it.

**2) What approach would you suggest to obtain minimum latency for gimbal control?**
For example I would like to achieve similar responsiveness of control like I would have with servo motors that are turning the plane control surfaces.
Should I go to the direct control via RC inputs or Mavlink commands are sufficient?

Thank you for your time.

Closed 2023-10-26.

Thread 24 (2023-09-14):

unable to calibrate "imu1 is not present or on healty!"

onlineapps-cloud, 2023-09-14:
hi, i tried to calibrate my gimbal, i have installed imu2, and he working as expected, but when i want to calibrate i cannot bypasss this erro, in wizard i disabled imu1 check, but not help :(
can anyone say, what i do wrong?
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

onlineapps-cloud, 2023-09-14:
in wiki http://www.olliw.eu/storm32bgc-wiki/Using_a_2nd_IMU
The calibration of the 2nd IMU works similar to the camera IMU; one just has to select the 2nd IMU in the respective fields.
but, this not work, i had errol that "imu1 is not present or on healty!"

onlineapps-cloud, 2023-09-14:
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

onlineapps-cloud, 2023-09-14:
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

onlineapps-cloud, 2023-09-14:
sorry, im newbie, i have only gimbal, i need additional camera with IMU? can you give some example?
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

onlineapps-cloud, 2023-09-14:
as i understand this sensor not workin, yes? IMU2 is accelerometer that is onboard, yes?

olliw42, 2023-09-14:
pl go first to the wiki, it will answer nearly all your questions ... you are expected to have spend sufficient time with the wiki, otherwise you will not get to anywhere with STorM32.

Read espeically also big red warning boxes, like this one here: http://www.olliw.eu/storm32bgc-wiki/Downloads

onlineapps-cloud, 2023-09-14:
i searched my IMU module, but i cannot find it here http://www.olliw.eu/storm32bgc-wiki/Overview_of_NT_Modules
my IMU module is not listed,
module close view. Model: INVENSENSE MPU-6050
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

Ensys NT Modules uses MPU-6050, which firmware i need to load, to work this IMU module?
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

onlineapps-cloud, 2023-09-14:
Also i want donate (if you accept donations) for future development (and for your great work!), i can pay in crypto only.

onlineapps-cloud, 2023-09-14:
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
now i understand why it will not work, i need firmware that will support this IMU device, yes? if yes, i don't know which firmware support this IMU module :(, i still reading  documentation :)

onlineapps-cloud, 2023-09-14:
yes, you are correct, firmware work as expected, my apologies!

Closed 2023-09-14.

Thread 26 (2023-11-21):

Can I control the gimbal through a raspberryPi without the hat?

Ncaso, 2023-11-21:
I'm working on a quad-copter project where I want all the commands for the gimbal controller to be sent through the onboard pi computer.
I am hoping to code something where the gimbal will receive inputs on where it should point and respond accordingly.
Is this something I can do with the Storm32 controller? Any advice or direction would be greatly appreciated :)

olliw42, 2023-11-21:
Hey Ncaso
first off, this here is not a support forum, but the place to report specific issues with materials provided in this repository. I thus will close this issue.
For support, questions, discusssions you can go the STorM32 thread at rcroups. I see that you already found that place. :+1:
So closing.

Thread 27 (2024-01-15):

CMD_GETDATAFIELDS result does not match documentation

vryabokon1705, 2024-01-15:
Version: v2.67e ll, OlliW 323BGC, v3.3 F103RC
https://www.olliw.eu/storm32bgc-wiki/Serial_Communication
Looks like CMD_GETDATAFIELDS serial command documentation is inaccurate. For example, if i use 0x0020 = LIVEDATA_IMU1ANGLES, i receive the same data as in Imu1AHRS.R.x, Imu1AHRS.R.y, Imu1AHRS.R.z from command CMD_GETDATA, and if i use 0x0010 = LIVEDATA_IMU1R, i receive the same data as in aImu1Angle.Pitch, aImu1Angle.Roll, aImu1Angle.Yaw
Plus if i want to use 0x0004 = LIVEDATA_IMU1GYRO and 0x0008 = LIVEDATA_IMU1ACC, i cannot find documentation how can i decode these data, CMD_GETDATA comman does not include LIVEDATA_IMU1GYRO and LIVEDATA_IMU1ACC

olliw42, 2024-01-15:
hey @vryabokon1705
many thx for the report, it's possible that the docs doesn't match, I haven't looked at it for some while. I will look into it.
can I ask: if you use CMD_GETDATA and the simple 'd' command, you do get the same data, and these data match the description for the 'd' command, right?

vryabokon1705, 2024-01-15:
Hi. I did not use d command yet, but CMD_GETDATA result looks like match description of data from 'd' command

olliw42, 2024-01-15:
ok, thanks.
I will look into it.

Closed 2024-01-15.

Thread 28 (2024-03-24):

Gerber Files for NT Modules (IMU)

natiz, 2024-03-24:
Hi @olliw42,

Thanks for this project! Glad to see its still active.

I have an old 1.31 board which I want to revive (been sitting in storage since 2015), and am looking for an NT IMU module for it, as I only have I2C IMUs, which are limited to the v0.96 firmware.
I saw the very limited options for [sourcing the NT modules](https://www.olliw.eu/storm32bgc-wiki/Where_to_get_NT_Modules), so I thought about maybe sourcing the board myself, via one of the PCB manufactures (such as JLPCB), which require Gerber files.
Would you be able to export those in Gerber format, for example for the [storm32-nt-imu-v42-g4](https://github.com/olliw42/storm32bgc/tree/master/storm32-nt)?

olliw42, 2024-03-24:
I haven't done that for a very long while and would have to relearn and work out what to do and what is needed essentially form scratch. I'm sorry to say that I won't find the time to do so in the near future.
I would think that with some web research there should be tools which allow you doing this. Eagle CAD is after all quite popular.
Sorry.

natiz, 2024-03-24:
Thanks for the quick response.

I’ll try to export it myself, should be possible according to [this](https://jlcpcb.com/help/article/9-How-to-Generate-Gerber-and-Drill-Files-in-Autodesk-Eagle).

Are there any other places that sell some version of the IMU?

olliw42, 2024-03-24:
ensys sometimes has some in stock

olliw42, 2024-03-26:
many THX
you coud consider doing a PR to add them in a subfolder storm32-nt/storm32-nt-logger-v2x-g4/gerber

natiz, 2024-03-26:
Sure https://github.com/olliw42/storm32bgc/pull/29

Closed 2024-03-26.

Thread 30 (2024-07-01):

NT logging bitmask include basic automatically

sheldonHe1996, 2024-07-01:
Hello, olliw;
   when i set nt logging bitmask only to include pid in option, it seems the basic logging data is also chosed.

olliw42, 2024-07-01:
there must be a minimum set of default logging data for the logging to work at all

pl note that the github issues are not for support questions, there is the rcgroups thread for that

closing since I believe no issue and question is answered. Thx for the comment.

Closed 2024-07-01.

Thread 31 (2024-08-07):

Which firmware should be used for burning the Storm32-nt-bgc-v41 board?

suiaiyun, 2024-08-07:
Hello, may I ask which firmware should be burned onto the Storm32-nt-bgc-v41 board? The corresponding board was not found in the GUI tool. Does this board already have firmware support?

olliw42, 2024-08-08:
this board is fully supported but it is not in a current release yet. Somewhere in the rcgroups thread there is a prerelease version posted (but I wouldn't know where to find it exactly). I'll plan to do a release next week if possible, it when should be in the GUI.

suiaiyun, 2024-08-13:
> this board is fully supported but it is not in a current release yet. Somewhere in the rcgroups thread there is a prerelease version posted (but I wouldn't know where to find it exactly). I'll plan to do a release next week if possible, it when should be in the GUI.

Great, looking forward to this release. Thank you.

sksrmsl, 2024-11-12:
I have two "storm32-nt-bgc-v41" boards.
I'm checking the operation.
The latest version of "o323BGCTool_v269e" does not contain "storm32-nt-bgc-v41" version of the HEX file.

Is there a way to check it out?
I would like to ask for your help

OrhanKoseoglu, 2024-11-22:
> this board is fully supported but it is not in a current release yet. Somewhere in the rcgroups thread there is a prerelease version posted (but I wouldn't know where to find it exactly). I'll plan to do a release next week if possible, it when should be in the GUI.

I can't find appropriate firmware for the v4.1 board?

OrhanKoseoglu, 2024-11-22:
> > this board is fully supported but it is not in a current release yet. Somewhere in the rcgroups thread there is a prerelease version posted (but I wouldn't know where to find it exactly). I'll plan to do a release next week if possible, it when should be in the GUI.
>
> Great, looking forward to this release. Thank you.

Did you find?

suiaiyun, 2024-11-23:
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

No, not yet. I'm waiting for Ollie to release it

zanefond, 2024-12-04:
Any news?

kami4ka, 2025-01-27:
Is it dead?

olliw42, 2025-05-02:
v4.1 firmware is included in latest release v2.70e

so closing

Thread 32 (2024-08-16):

downgrading to a single-axis gimbal

Shen-LW, 2024-08-16:
I want to fix the roll and yaw, stabilizing only the pitch, similar to downgrading to a single-axis gimbal. What modifications do I need to make?

olliw42, 2024-08-16:
this github repository is NOT for support questions. Pl choose the rcgroups discussion thread.

hint: there is also a wiki, and reading it can be very benefitial.

closing since no issue but support.

Shen-LW, 2024-08-19:
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

Thank you for your reply. I understand now.

Closed 2024-08-16.

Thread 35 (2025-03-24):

BGC v90 mit Arducopter nutzbar?

Rothammel, 2025-03-24:
habe einen alten Gimbal, kann man den nutzen? ich habe mav1 eingerichtet und kann ihn im MP als zweite Komponente auswählen und dort steuern, RC Input gelingt mir aber nicht

olliw42, 2025-03-25:
es gibt kein "BGC v90" im STorM32 Ecosystem. Die Vermutung liegt also nahe das es sich um kein STorM32 Gimbal sondern etwas Anderes handelt und du hier mit deinen Fragen am falschen Ort bist.
Zudem sind github issues nicht für allgemeine Supportfragen gedacht. Dafür gibt es entsprechende Threads etc. pp auf rcgroups. Ohne mehr/bessere Infos um welches Gimbal du hast wirst du aber auch dort keine besseren Antqqorten bekommen.

Da es sich um kein Issue sondern Support handelt, schliesse ich das hier.

Rothammel, 2025-03-25:
danke für deine Antwort. es ist ein Board V1.3 mit Firmware 0.90. ich bekomme keine serielle Verbindung zum laufen, nur Mavlink. Mavlink selber läuft aber auch nicht gut und funktioniert auch nicht mit den Ardupilot Gimbal Funktionen.

ich habe noch etliche dieser Gimbals und auch Aliexpress verkauft sie noch immer.
wo kann ich die V0.96 Quellen ansehen?

olliw42, 2025-03-25:
> Board V1.3 mit Firmware 0.90

ok ... dir ist klar dass das uralt ist (auch v0.96 ist uralt), und daher (schon laaaannnggeeee) nicht mehr supported wird. Sorry man, time goes on.

>  ich bekomme keine serielle Verbindung zum laufen, nur Mavlink. Mavlink selber läuft aber auch nicht gut und funktioniert auch nicht mit den Ardupilot Gimbal Funktionen.

da kann ich nichts zu sagen, kann alles mögliche sein. Musste dir selber deinen Weg mit hilfe des Wikis und der ArduPilot docs suchen, oder jemand finden der das benutzt.

> auch Aliexpress verkauft sie noch immer.

was nicht heist dass das aktuell wäre ...

> wo kann ich die V0.96 Quellen ansehen?

nirgends

Rothammel, 2025-03-25:
Vielen Dank für die Infos. Leider kann ich aktuelle Boards mit aktueller Firmen nirgendwo kaufen. Ich habe noch etliche dieser gimbles und sie funktionieren einwandfrei an einem copter und auch an Flugzeugen. ich würde sie schon gerne verwenden

Closed 2025-03-25.

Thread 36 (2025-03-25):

Serial CRC wird nicht ausgewertet

Rothammel, 2025-03-25:
Hallo OlliW,

ich habe etliche V1.3x Gimbals, geupdatet mit V0.96.
nun habe ich mich mal mit der seriellen Verbindung beschäftigt.
folgendes ist mir aufgefallen:
- egal welchen CRC ich sende, ich erhalte immer ein Byte 3: 00, also laut: [](https://www.olliw.eu/storm32bgc-v1-wiki/Serial_Communication)
0 = SERIALRCCMD_ACK_OK
der gimbal führt den Pitch Winkel dann auch aus.

hier die debug Ausgabe:
```
Serielle Verbindung hergestellt
250
14
17
0
0
248
193
0
0
0
0
0
0
0
0
0
0
0
0
111
Pitch-Winkel gesendet: -31 °
Antwort erhalten:
Byte 0: FB (û)
Byte 1: 01 ( )
Byte 2: 96 ()
Byte 3: 00 (
Byte 4: 62 (b)
Byte 5: 2E (.)
```

hier mein Code, ist nur schnell in PureBasic zusammengeklopft:

```
; Funktion zur Berechnung der X25 CRC-16 Prüfsumme
Procedure.i CRC16_X25(*data, length)
  Protected crc.l = $FFFF
  Protected i, j

  For i = 1 To length - 1
  ;For i = 0 To length - 1
    crc ! (PeekA(*data + i) << 8)
    For j = 0 To 7
      If crc & $8000
        crc = (crc << 1) ! $1021
      Else
        crc << 1
      EndIf
    Next
  Next

  ProcedureReturn crc & $FFFF
EndProcedure

; Funktion zur Konvertierung von Float zu Byte-Array
Procedure ConvertFloatToBytes(float.f, *bytes)
  CopyMemory(@float, *bytes, SizeOf(Float))  ; Konvertiere Float in 4 Byte
EndProcedure

; Öffne die serielle Schnittstelle mit Puffern
If OpenSerialPort(0, "COM5", 115200, #PB_SerialPort_NoParity, 8, 1, #PB_SerialPort_NoHandshake, 1024, 1024)
  Debug "Serielle Verbindung hergestellt"

  ; Befehls-Array vorbereiten
  Dim command.a(19)
  command(0) = $FA  ; Start-Byte
  command(1) = $0E  ; Längenbyte
  command(2) = $11  ; CMD_SETANGLE

  pitchAngle = Random(90, 0) -45
  rollAngle = 0.0
  yawAngle = 0.0

  ; Konvertiere die Floats und füge sie in das Array ein
  ConvertFloatToBytes(pitchAngle, @command(3))  ; Pitch in Bytes (4 Byte)
  ConvertFloatToBytes(rollAngle, @command(7))   ; Roll in Bytes (4 Byte)
  ConvertFloatToBytes(yawAngle, @command(11))   ; Yaw in Bytes (4 Byte)

  command(15) = $00   ; Flag-Byte
  command(16) = $00   ; Typ-Byte

  ; Prüfsumme berechnen
  crc.i = CRC16_X25(@command(0), 16)
  ;command(17) = crc & $FF  ; CRC Low-Byte
  command(17) = $00
  ;command(18) = (crc >> 8) & $FF  ; CRC High-Byte
  command(18) = $00
  command (19) = $6F

  For i = 0 To 19
    Debug command(i)
  Next
  ; Befehl senden
  If WriteSerialPortData(0, @command(0), 19)
    Debug "Pitch-Winkel gesendet: " + Str(pitchAngle) + " °"
  Else
    Debug "Fehler beim Senden der Daten"
  EndIf

  Delay(500)

  ; Prüfen, ob Daten verfügbar sind
  responseLength = AvailableSerialPortInput(0)
  If responseLength > 0
    Dim response.a(responseLength - 1)
    ReadSerialPortData(0, @response(0), responseLength)

    Debug "Antwort erhalten: "
    For i = 0 To responseLength - 1
      Debug "Byte " + Str(i) + ": " + RSet(Hex(response(i)), 2, "0") + " (" + Chr(response(i)) + ")"
    Next
  Else
    Debug "Keine Antwort erhalten."
  EndIf

  CloseSerialPort(0)
Else
  Debug "Fehler beim Öffnen der seriellen Schnittstelle"
EndIf

```

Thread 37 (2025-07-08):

Questions about v4. x IMU board crystal oscillator

suiaiyun, 2025-07-08:
May I ask if the crystal oscillator used in the v4. x version of the IMU board must be an active crystal oscillator? Will using a passive crystal oscillator cause the IMU board to malfunction?

olliw42, 2025-07-09:
it needs to be that or a technically similar type
tcxo with cmos output

Closed 2025-07-09.

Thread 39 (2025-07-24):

Servo pitch motor usage

xeom500k, 2025-07-24:
Hello
I am using storm 32 v4.1 to balance the barrel for the tank.Can I leave the pitch shaft as servo kst bls815 And yaw is the gimbal motor to rotate the barrel But when I set pitch to servo then press writer+store then reconnect, oh The servo tab is not lit, and when entering the gimbal configurator, it shows not connected to board and then the Pitch motor usage section automatically switches back disabled  I have motor mapping as pitch Yaw roll and plug the servo into pin mot1
Please help me fix this problem, thank you very much everyone.

xeom500k, 2025-07-25:
Hi
I want to use Storm32-Link to output orientation data to an Arduino, so the
Arduino can control the servo motor for the pitch axis only. Meanwhile, the
yaw axis will be controlled directly by a gimbal motor through the Storm32
controller. Is this setup possible and effective?"

Vào 14:16 Th 6, 25 thg 7, 2025 olliw42 ***@***.***> đã viết:

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

xeom500k, 2025-07-25:
Hi
I want to use Storm32-Link to output orientation data to an Arduino, so the Arduino can control the servo motor for the pitch axis only. Meanwhile, the yaw axis will be controlled directly by a gimbal motor through the Storm32 controller. Is this setup possible and effective?"

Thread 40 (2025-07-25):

Configure IMU2 as main imu

jtheodore15, 2025-07-25:
Hello,
i was trying to set IMU2 (on board) as main IMU. My BGC is embedded on the camera (depend of motor mouvement).

Is there any mossibility ?
thnak you very much for your answer
Regards
Julien

olliw42, 2025-07-25:
no

Closed 2025-07-25.

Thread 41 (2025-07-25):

Nt imu 4.2

xeom500k, 2025-07-25:
Hi
Please help me
After flashing the firmware to my NT IMU 4.2, the green LED lights up steadily, indicating that the flash process completed. However, once I reconnect the IMU, only the red LED remains on continuously, and the green LED does not light up anymore. Additionally, the IMU becomes slightly warm to the touch after a short time. It seems like the firmware might not be running correctly on the device.I flashed firmware v2.73e on sotmr32 v4.1 and 0.56e on imu
thank you very much

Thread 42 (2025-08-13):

PERL2EXE error when trying to flash firmware onto the v6.2 bgc board for the first time.

Sridhar701Pitt, 2025-08-13:
Config:
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

Error:
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

Flashing a v6.2 bgc board for the first time using Systembootloader. Following first time flashing instructions: https://www.olliw.eu/storm32bgc-v2-wiki/How_to_flash_firmware#First-Time_Flashing

Clicking OK and proceeding with flashing seems to work fine. Board is properly detected.

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

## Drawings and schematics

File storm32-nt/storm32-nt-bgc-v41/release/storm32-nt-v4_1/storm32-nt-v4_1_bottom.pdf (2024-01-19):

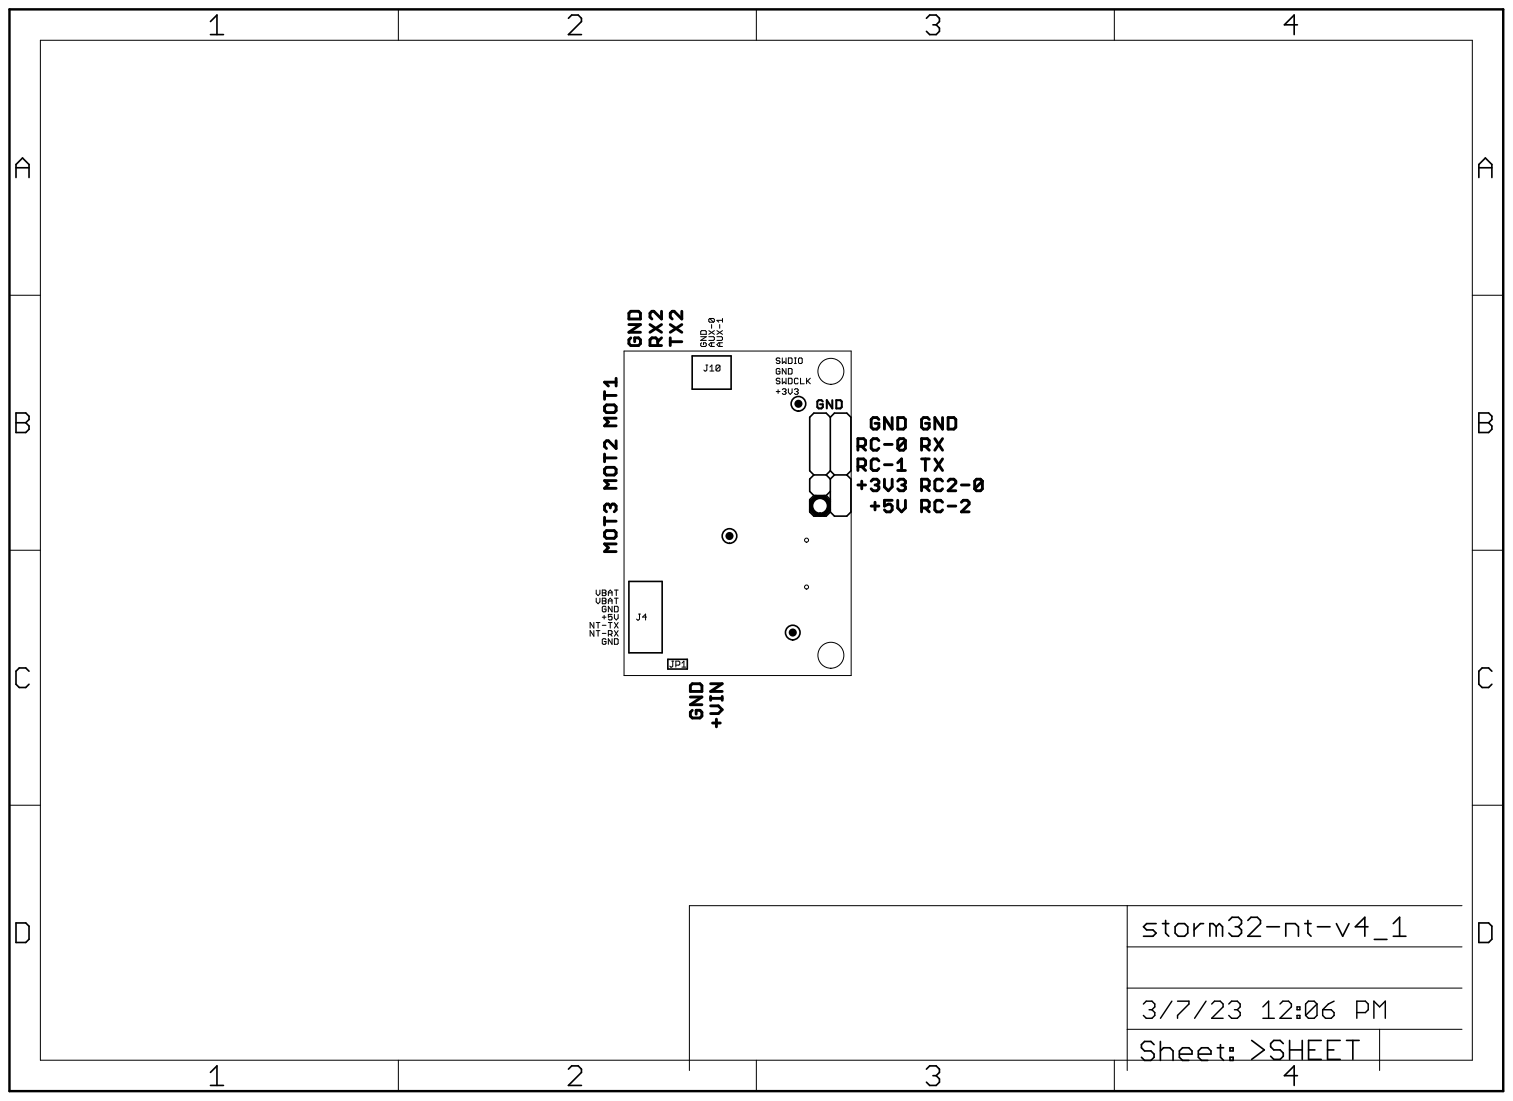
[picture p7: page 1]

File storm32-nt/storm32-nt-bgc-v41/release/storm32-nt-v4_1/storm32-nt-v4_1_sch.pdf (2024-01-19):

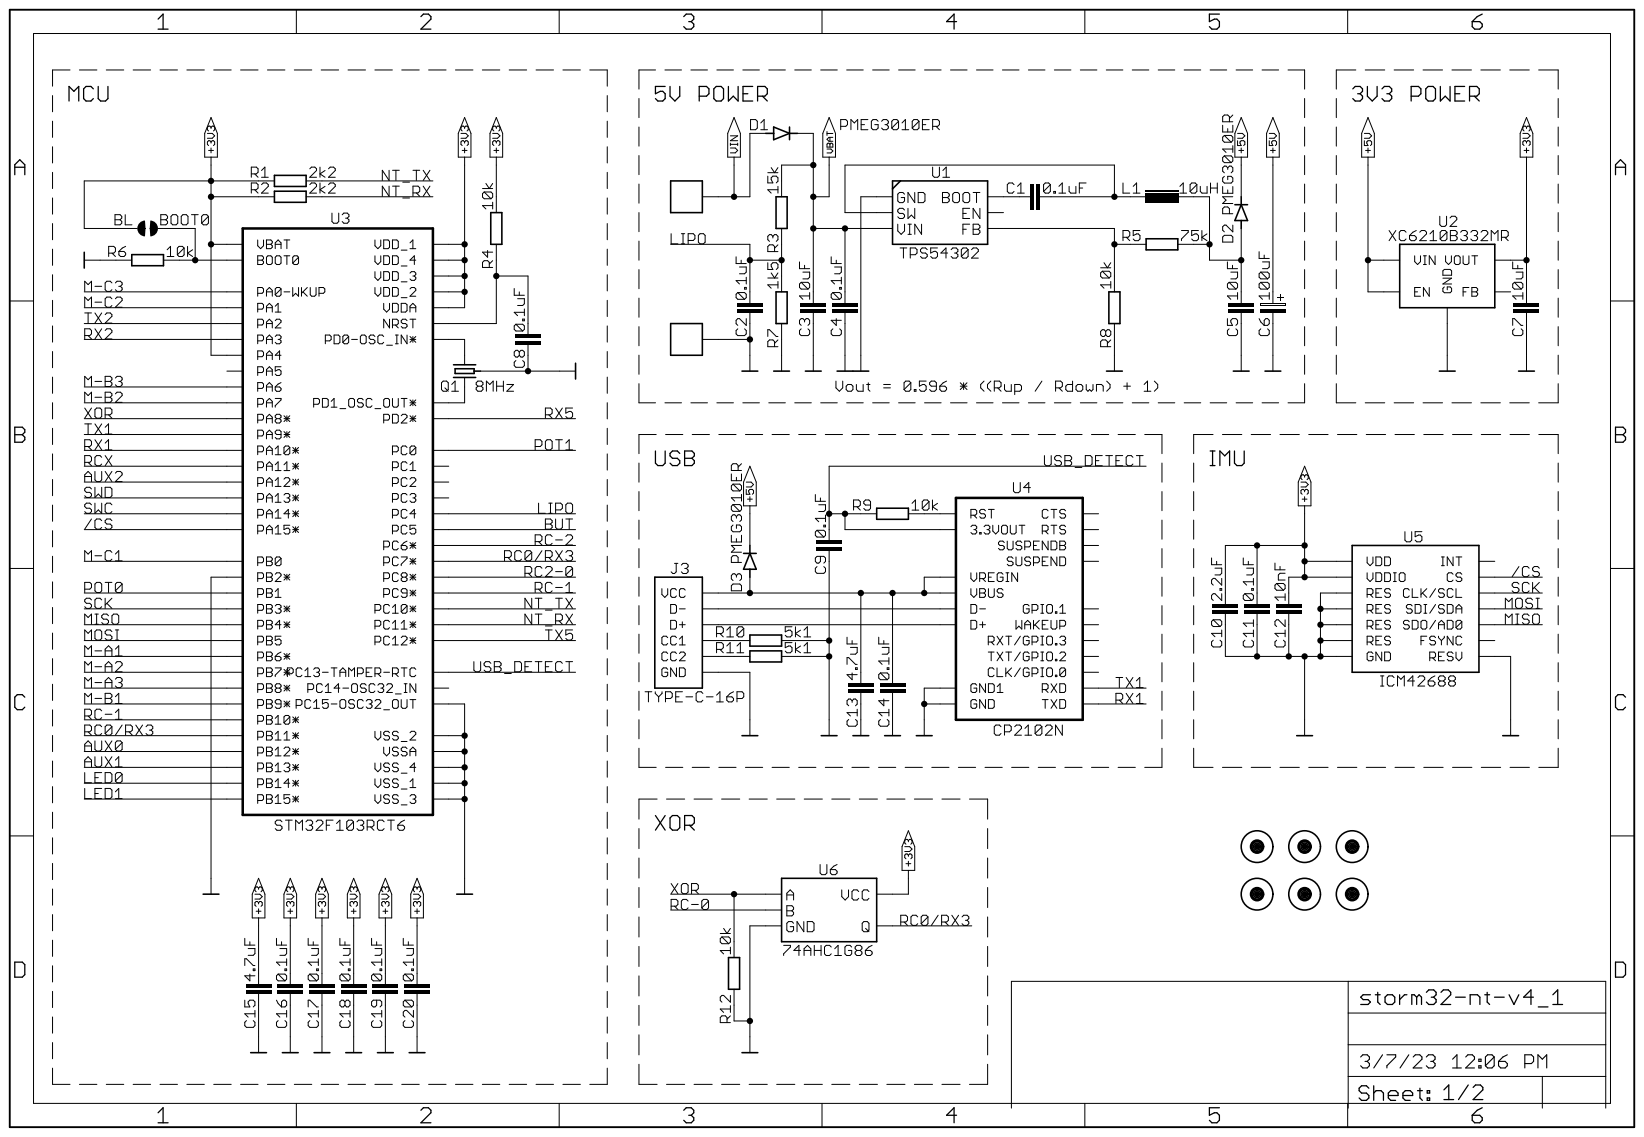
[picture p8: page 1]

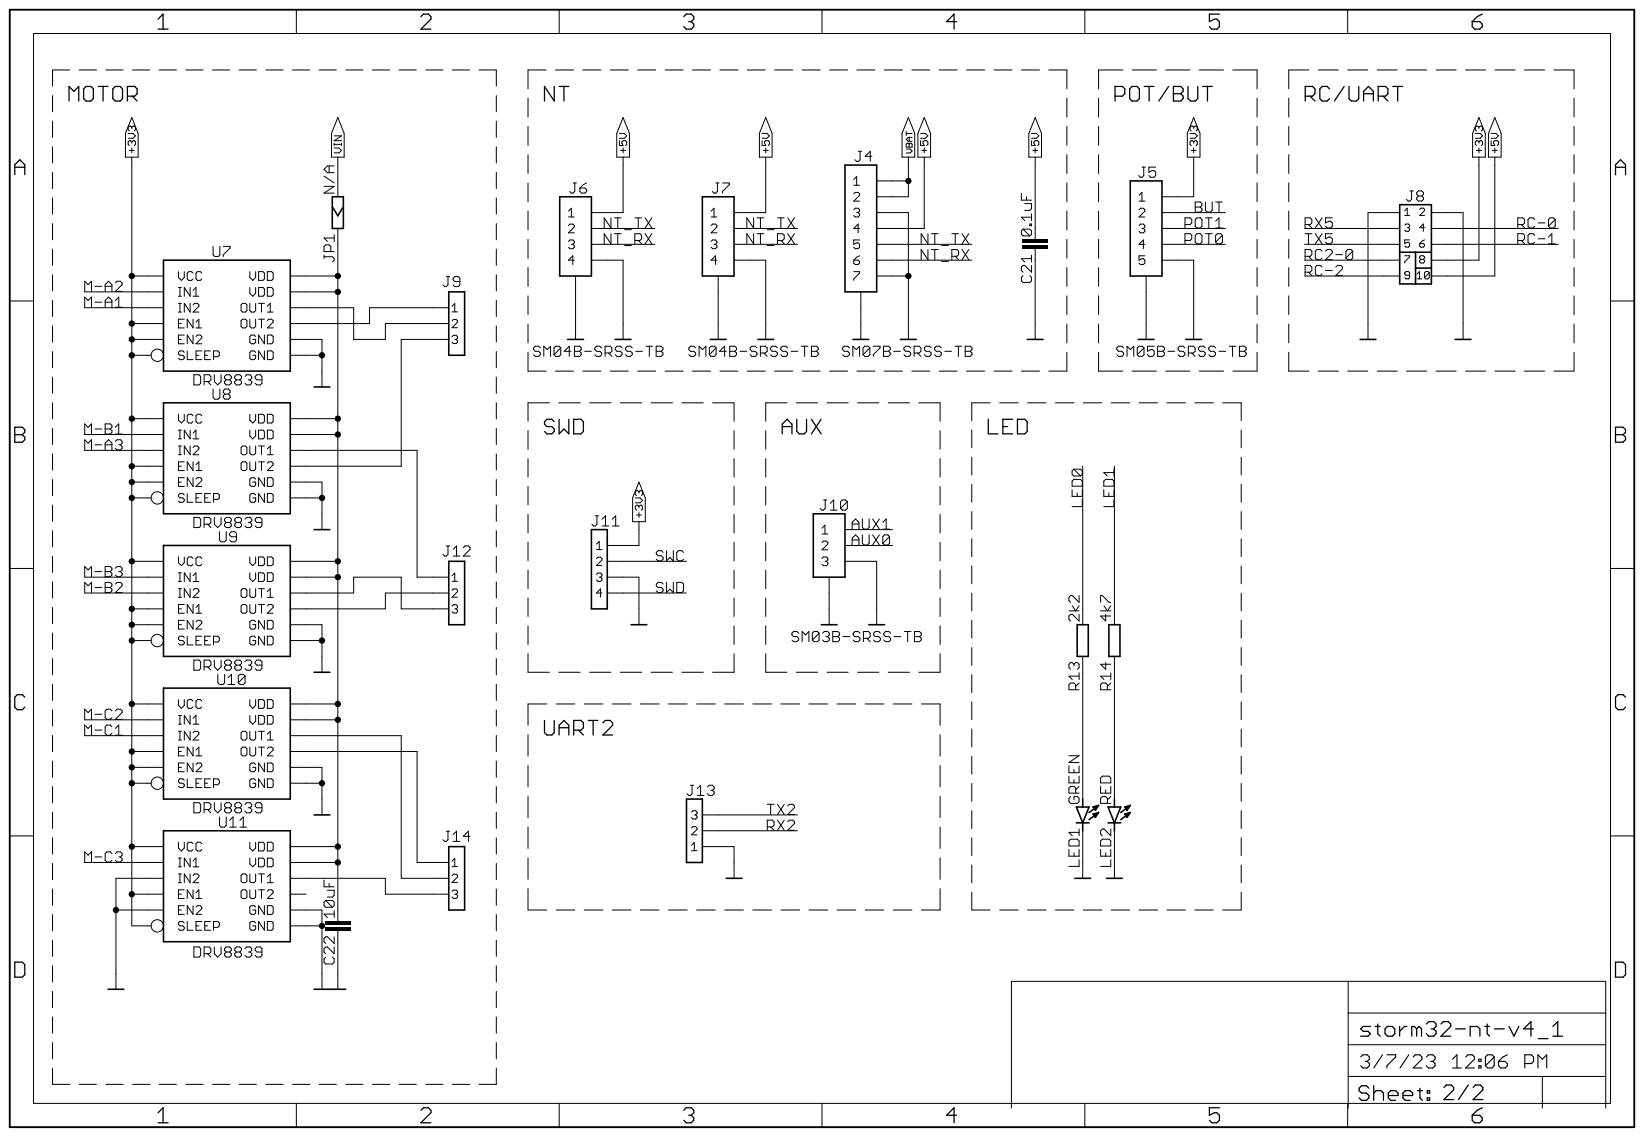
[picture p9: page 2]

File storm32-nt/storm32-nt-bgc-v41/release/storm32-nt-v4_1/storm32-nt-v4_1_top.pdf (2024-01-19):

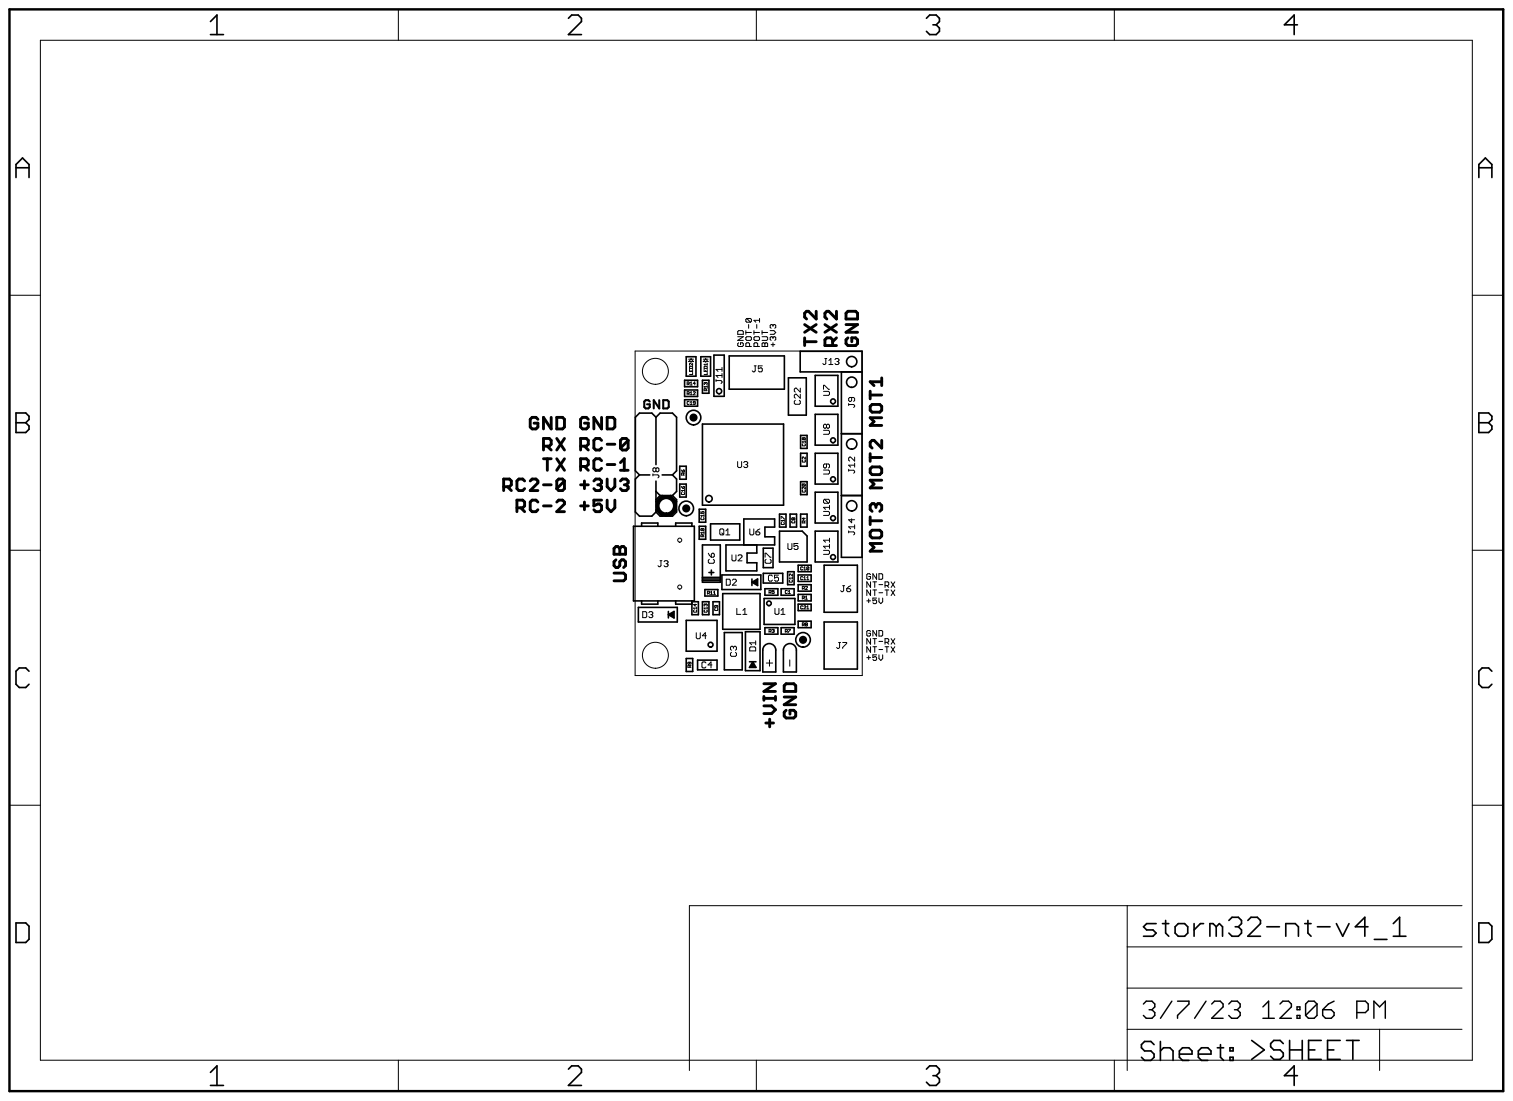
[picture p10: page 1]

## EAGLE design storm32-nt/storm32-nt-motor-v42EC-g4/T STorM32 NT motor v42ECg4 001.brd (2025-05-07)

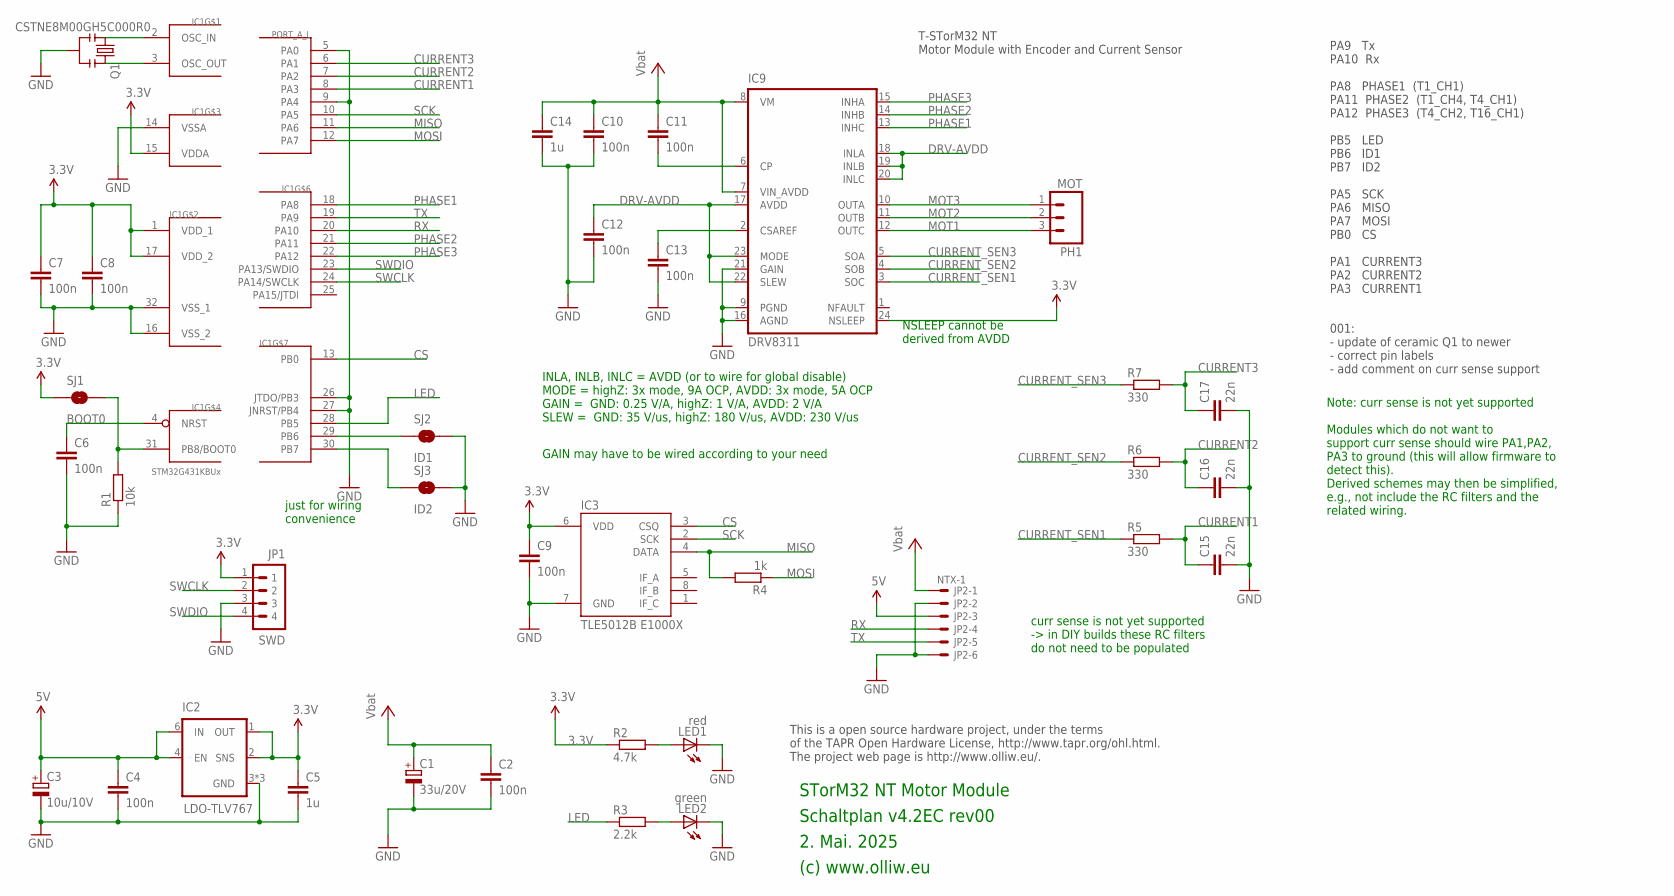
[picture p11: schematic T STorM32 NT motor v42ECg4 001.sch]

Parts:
C1: 33u/20V; SMC_C
C2, C4: 100n; C0603
C3: 10u/10V; SMC_B
C5, C14: 1u; C0603
C6, C7, C8, C9, C10, C11, C12, C13: 100n; C0402
C15, C16, C17: 22n; C0402
IC1: STM32G431KBUx; UFQFPN32
IC2: LDO-TLV767; WSON-6-2X2
IC3: TLE5012B E1000X; SO08
IC9: DRV8311; QFN(WQFN)24-3X3-DRV8311
JP1: SWD; 4X1_1P27_OCT_BILEX
JP2: NTX-1; SM06B-SRSS-TB
LED1: red; CHIPLED_0603
LED2: green; CHIPLED_0603
PH1: MOT; 1X03_NO_SILK
Q1: CSTNE8M00GH5C000R0; RESONATOR-SMD
R1: 10k; R0402
R2: 4.7k; R0402
R3: 2.2k; R0402
R4: 1k; R0402
R5, R6, R7: 330; R0402
SJ1: BOOT0; SJ_2S-NO
SJ2: ID1; SJ_2S-NO
SJ3: ID2; SJ_2S-NO

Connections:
3.3V: C5.1, C7.1, C8.1, C9.1, IC1.1 (VDD_1), IC1.15 (VDDA), IC1.17 (VDD_2), IC2.1 (OUT), IC2.2 (SNS), IC3.6 (VDD), IC9.24 (NSLEEP), JP1.1, R2.1, SJ1.1
5V: C3.+, C4.1, IC2.4 (EN), IC2.6 (IN), JP2.3
CS: IC1.13 (PB0), IC3.3 (CSQ)
CURRENT1: C15.1, IC1.8 (PA3), R5.2
CURRENT2: C16.1, IC1.7 (PA2), R6.2
CURRENT3: C17.1, IC1.6 (PA1), R7.2
CURRENT_SEN1: IC9.3 (SOC), R5.1
CURRENT_SEN2: IC9.4 (SOB), R6.1
CURRENT_SEN3: IC9.5 (SOA), R7.1
DRV-AVDD: C12.1, IC9.17 (AVDD), IC9.18 (INLA), IC9.19 (INLB), IC9.20 (INLC), IC9.22 (SLEW), IC9.23 (MODE)
DRV-CP: C11.2, IC9.6 (CP)
DRV-CSAREF: C13.1, IC9.2 (CSAREF)
GND: C1.-, C2.2, C3.-, C4.2, C5.2, C6.2, C7.2, C8.2, C9.2, C10.2, C12.2, C13.2, C14.2, C15.2, C16.2, C17.2, IC1.5 (PA0), IC1.9 (PA4), IC1.14 (VSSA), IC1.16 (VSS_2), IC1.26 (JTDO/PB3), IC1.27 (JNRST/PB4), IC1.32 (VSS_1), IC2.3 (GND), IC2.5 (GND), IC2.7 (GND), IC3.7 (GND), IC9.9 (PGND), IC9.16 (AGND), IC9.21 (GAIN), JP1.3, JP2.2, JP2.6, LED1.C, LED2.C, Q1.2, R1.1, SJ2.2, SJ3.2
ID1: IC1.29 (PB6), SJ2.1
ID2: IC1.30 (PB7), SJ3.1
LED: IC1.28 (PB5), R3.1
MISO: IC1.11 (PA6), IC3.4 (DATA), R4.2
MOSI: IC1.12 (PA7), R4.1
MOT1: IC9.12 (OUTC), PH1.3
MOT2: IC9.11 (OUTB), PH1.2
MOT3: IC9.10 (OUTA), PH1.1
unnamed: C6.1, IC1.4 (NRST)
unnamed: IC1.31 (PB8/BOOT0), R1.2, SJ1.2
unnamed: IC1.2 (OSC_IN), Q1.1
unnamed: IC1.3 (OSC_OUT), Q1.3
unnamed: LED1.A, R2.2
unnamed: LED2.A, R3.2
PHASE1: IC1.18 (PA8), IC9.13 (INHC)
PHASE2: IC1.21 (PA11), IC9.14 (INHB)
PHASE3: IC1.22 (PA12), IC9.15 (INHA)
RX: IC1.20 (PA10), JP2.4
SCK: IC1.10 (PA5), IC3.2 (SCK)
SWCLK: IC1.24 (PA14/SWCLK), JP1.2
SWDIO: IC1.23 (PA13/SWDIO), JP1.4
TX: IC1.19 (PA9), JP2.5
VBAT: C1.+, C2.1, C10.1, C11.1, C14.1, IC9.7 (VIN_AVDD), IC9.8 (VM), JP2.1

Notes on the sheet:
2. Mai. 2025
(c) www.olliw.eu
STorM32 NT Motor Module
Schaltplan v4.2EC rev00
This is a open source hardware project, under the terms of the TAPR Open Hardware License, http://www.tapr.org/ohl.html. The project web page is http://www.olliw.eu/.
T-STorM32 NT Motor Module with Encoder and Current Sensor
PA9 Tx PA10 Rx PA8 PHASE1 (T1_CH1) PA11 PHASE2 (T1_CH4, T4_CH1) PA12 PHASE3 (T4_CH2, T16_CH1) PB5 LED PB6 ID1 PB7 ID2 PA5 SCK PA6 MISO PA7 MOSI PB0 CS PA1 CURRENT3 PA2 CURRENT2 PA3 CURRENT1
INLA, INLB, INLC = AVDD (or to wire for global disable) MODE = highZ: 3x mode, 9A OCP, AVDD: 3x mode, 5A OCP GAIN = GND: 0.25 V/A, highZ: 1 V/A, AVDD: 2 V/A SLEW = GND: 35 V/us, highZ: 180 V/us, AVDD: 230 V/us
NSLEEP cannot be derived from AVDD
just for wiring convenience
curr sense is not yet supported -> in DIY builds these RC filters do not need to be populated
001: - update of ceramic Q1 to newer - correct pin labels - add comment on curr sense support
GAIN may have to be wired according to your need
Note: curr sense is not yet supported Modules which do not want to support curr sense should wire PA1,PA2, PA3 to ground (this will allow firmware to detect this). Derived schemes may then be simplified, e.g., not include the RC filters and the related wiring.

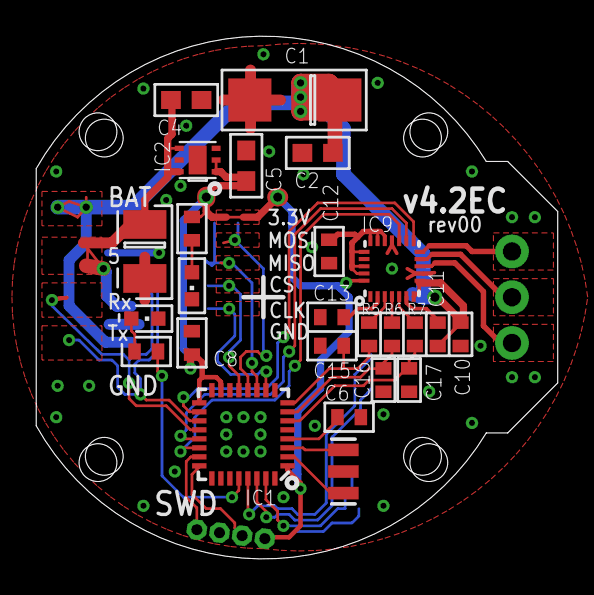
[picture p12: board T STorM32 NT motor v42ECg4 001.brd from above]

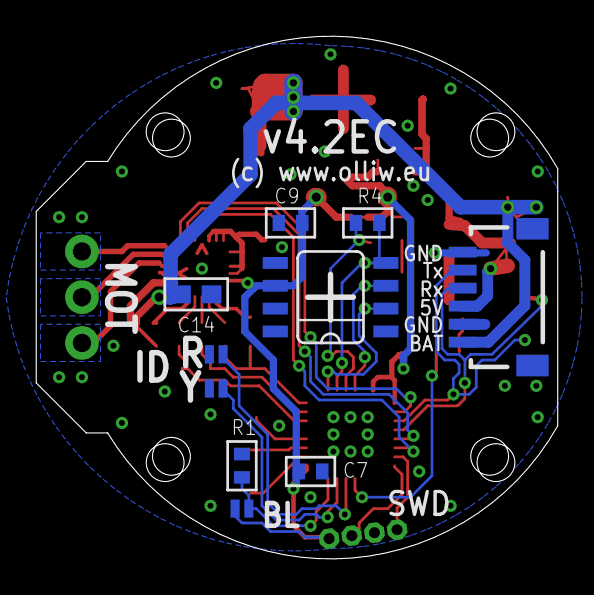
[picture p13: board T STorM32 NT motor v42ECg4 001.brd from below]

Board: 2 copper layers, 29.0 x 29.0 mm, 37 parts (10 on the bottom side), 36 nets.

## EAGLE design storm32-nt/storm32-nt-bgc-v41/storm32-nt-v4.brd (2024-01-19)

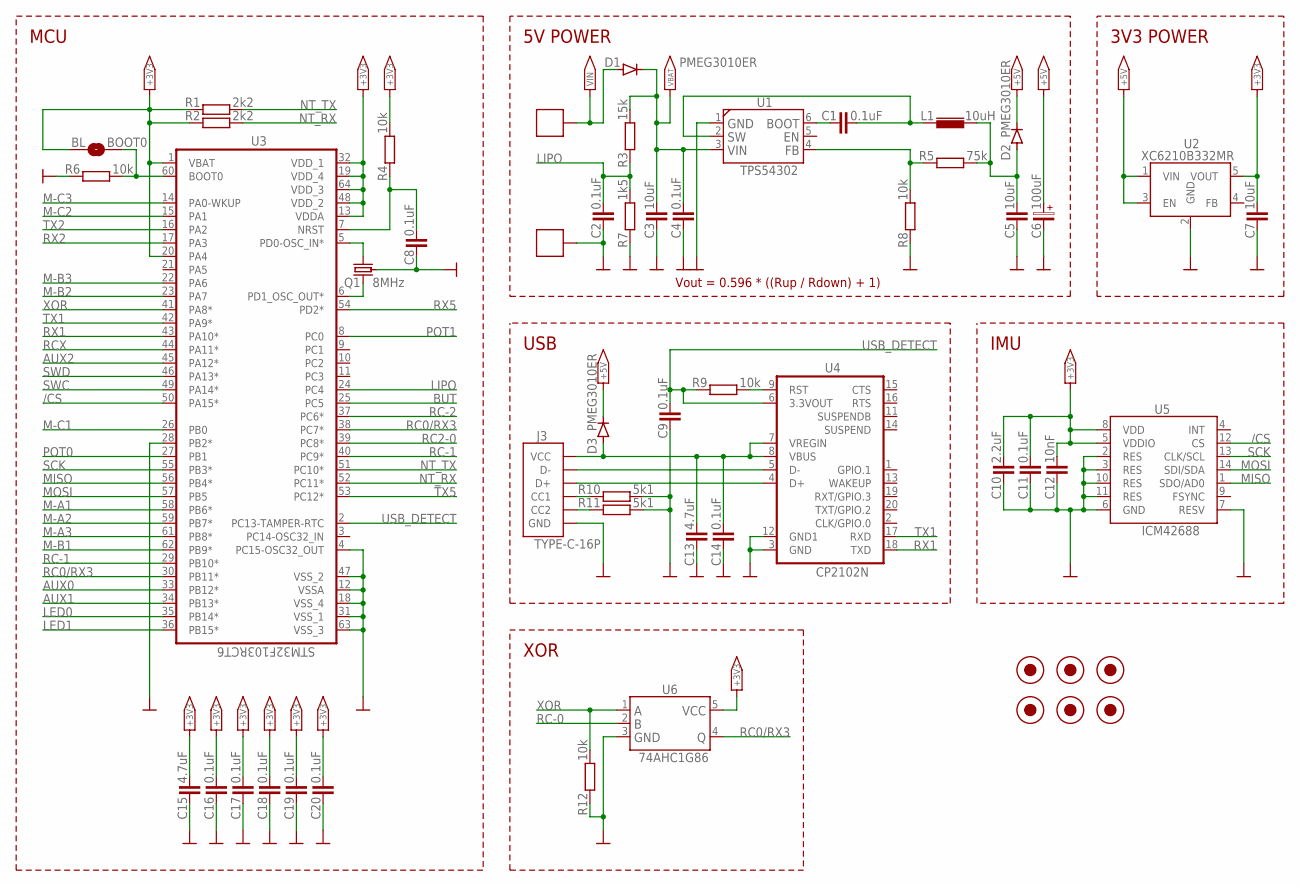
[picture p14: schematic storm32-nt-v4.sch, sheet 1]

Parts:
BL: BOOT0; __SPARKFUN2_SJ_2S-NO
C1, C2, C8, C9, C11, C14, C16, C17, C18, C19, C20: 0.1uF; 0402[1005-METRIC]
C3: 10uF; 1206[3216-METRIC]; VOLTAGE 63; MOUSER 81-GRM32ER71J106MA2L
C4: 0.1uF; 0603[1608-METRIC]
C5, C7: 10uF; 0603[1608-METRIC]
C6: 100uF; 1206[3216-METRIC]-POL
C10: 2.2uF; 0402[1005-METRIC]
C12: 10nF; 0402[1005-METRIC]
C13, C15: 4.7uF; 0402[1005-METRIC]
D1, D2, D3: PMEG3010ER; SOD-123
FIDUCIAL1, FIDUCIAL2, FIDUCIAL3, FIDUCIAL4, FIDUCIAL5, FIDUCIAL6: FIDUCIAL
J1: +; 1
J2: -; 1
J3: TYPE-C-16P
L1: 10uH; 4X4
Q1: 8MHz; RESONATOR
R1, R2: 2k2; 0402[1005-METRIC]
R3: 15k; 0402[1005-METRIC]
R4, R6, R8, R9, R12: 10k; 0402[1005-METRIC]
R5: 75k; 0402[1005-METRIC]
R7: 1k5; 0402[1005-METRIC]
R10, R11: 5k1; 0402[1005-METRIC]
U1: TPS54302; SOT-23-6
U2: XC6210B332MR; SOT-23-5
U3: STM32F103RCT6; QFP50P1200X1200X160-64N
U4: CP2102N; QFN-20
U5: ICM42688; LGA14
U6: 74AHC1G86; SOT-23-5

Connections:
+3V3: BL.2, C7.P$1 (1), C10.P$1 (1), C11.P$1 (1), C12.P$1 (1), C15.P$1 (1), C16.P$1 (1), C17.P$1 (1), C18.P$1 (1), C19.P$1 (1), C20.P$1 (1), R1.P$1, R2.P$1, R4.P$2, U2.5 (VOUT), U3.1 (VBAT), U3.13 (VDDA), U3.19 (VDD_4), U3.20 (PA4), U3.32 (VDD_1), U3.48 (VDD_2), U3.64 (VDD_3), U5.5 (VDDIO), U5.8 (VDD), U6.5; also elsewhere on the board
+5V: C6.P, D2.C, D3.C, U2.1 (VIN), U2.3 (EN); also elsewhere on the board
/CS: U3.50 (PA15*), U5.12 (CS)
AUX0: U3.33 (PB12*); also elsewhere on the board
AUX1: U3.34 (PB13*); also elsewhere on the board
AUX2: U3.45 (PA12*)
BUT: U3.25 (PC5); also elsewhere on the board
GND: C2.P$2 (2), C3.P$2 (2), C4.P$2 (2), C5.P$2 (2), C6.N, C7.P$2 (2), C8.P$2 (2), C9.P$2 (2), C10.P$2 (2), C11.P$2 (2), C12.P$2 (2), C13.P$2 (2), C14.P$2 (2), C15.P$2 (2), C16.P$2 (2), C17.P$2 (2), C18.P$2 (2), C19.P$2 (2), C20.P$2 (2), J2.1, J2.1A, J3.A1 (GND), J3.A12 (GND), J3.B1 (GND), J3.B12 (GND), J3.G1 (GND), J3.G2 (GND), J3.G3 (GND), J3.G4 (GND), Q1.G (GND), R6.P$1, R7.P$1, R8.P$1, R10.P$2, R11.P$2, R12.P$2, U1.1, U2.2 (GND), U3.4 (PC15-OSC32_OUT), U3.12 (VSSA), U3.18 (VSS_4), U3.28 (PB2*), U3.31 (VSS_1), U3.47 (VSS_2), U3.63 (VSS_3), U4.3 (GND), U4.12 (GND1), U5.2 (RES), U5.3 (RES), U5.6 (GND), U5.7 (RESV), U5.10 (RES), U5.11 (RES), U6.3; also elsewhere on the board
LED0: U3.35 (PB14*); also elsewhere on the board
LED1: U3.36 (PB15*); also elsewhere on the board
LIPO: C2.P$1 (1), R3.P$1, R7.P$2, U3.24 (PC4)
M-A1: U3.58 (PB6*); also elsewhere on the board
M-A2: U3.59 (PB7*); also elsewhere on the board
M-A3: U3.61 (PB8*); also elsewhere on the board
M-B1: U3.62 (PB9*); also elsewhere on the board
M-B2: U3.23 (PA7); also elsewhere on the board
M-B3: U3.22 (PA6); also elsewhere on the board
M-C1: U3.26 (PB0); also elsewhere on the board
M-C2: U3.15 (PA1); also elsewhere on the board
M-C3: U3.14 (PA0-WKUP); also elsewhere on the board
MISO: U3.56 (PB4*), U5.1 (SDO/AD0)
MOSI: U3.57 (PB5), U5.14 (SDI/SDA)
unnamed: J3.A5 (CC1), R10.P$1
unnamed: J3.B5 (CC2), R11.P$1
unnamed: C1.P$1 (1), L1.1, U1.2
unnamed: Q1.1, U3.6 (PD1_OSC_OUT*)
unnamed: Q1.2, U3.5 (PD0-OSC_IN*)
unnamed: C8.P$1 (1), R4.P$1, U3.7 (NRST)
unnamed: C1.P$2 (2), U1.6
unnamed: J3.A6 (D+), J3.B6 (D+), U4.4 (D+)
unnamed: J3.A7 (D-), J3.B7 (D-), U4.5 (D-)
unnamed: C13.P$1 (1), C14.P$1 (1), D3.A, J3.A4 (VCC), J3.A9 (VCC), J3.B4 (VCC), J3.B9 (VCC), U4.7 (VREGIN), U4.8 (VBUS)
unnamed: R9.P$2, U4.9 (RST)
unnamed: R5.P$1, R8.P$2, U1.4
unnamed: C5.P$1 (1), D2.A, L1.2, R5.P$2
unnamed: BL.1, R6.P$2, U3.60 (BOOT0)
NT_RX: R2.P$2, U3.52 (PC11*); also elsewhere on the board
NT_TX: R1.P$2, U3.51 (PC10*); also elsewhere on the board
POT0: U3.27 (PB1); also elsewhere on the board
POT1: U3.8 (PC0); also elsewhere on the board
RC0/RX3: U3.30 (PB11*), U3.38 (PC7*), U6.4
RC2-0: U3.39 (PC8*); also elsewhere on the board
RC-0: U6.2; also elsewhere on the board
RC-1: U3.29 (PB10*), U3.40 (PC9*); also elsewhere on the board
RC-2: U3.37 (PC6*); also elsewhere on the board
RCX: U3.44 (PA11*)
RX1: U3.43 (PA10*), U4.18 (TXD)
RX2: U3.17 (PA3); also elsewhere on the board
RX5: U3.54 (PD2*); also elsewhere on the board
SCK: U3.55 (PB3*), U5.13 (CLK/SCL)
SWC: U3.49 (PA14*); also elsewhere on the board
SWD: U3.46 (PA13*); also elsewhere on the board
TX1: U3.42 (PA9*), U4.17 (RXD)
TX2: U3.16 (PA2); also elsewhere on the board
TX5: U3.53 (PC12*); also elsewhere on the board
USB_DETECT: C9.P$1 (1), R9.P$1, U3.2 (PC13-TAMPER-RTC), U4.6 (3.3VOUT)
VBAT: C3.P$1 (1), C4.P$1 (1), D1.C, R3.P$2, U1.3; also elsewhere on the board
VIN: D1.A, J1.1, J1.1A; also elsewhere on the board
XOR: R12.P$1, U3.41 (PA8*), U6.1

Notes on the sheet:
Vout = 0.596 * ((Rup / Rdown) + 1)
5V POWER
USB
3V3 POWER
MCU
IMU
XOR

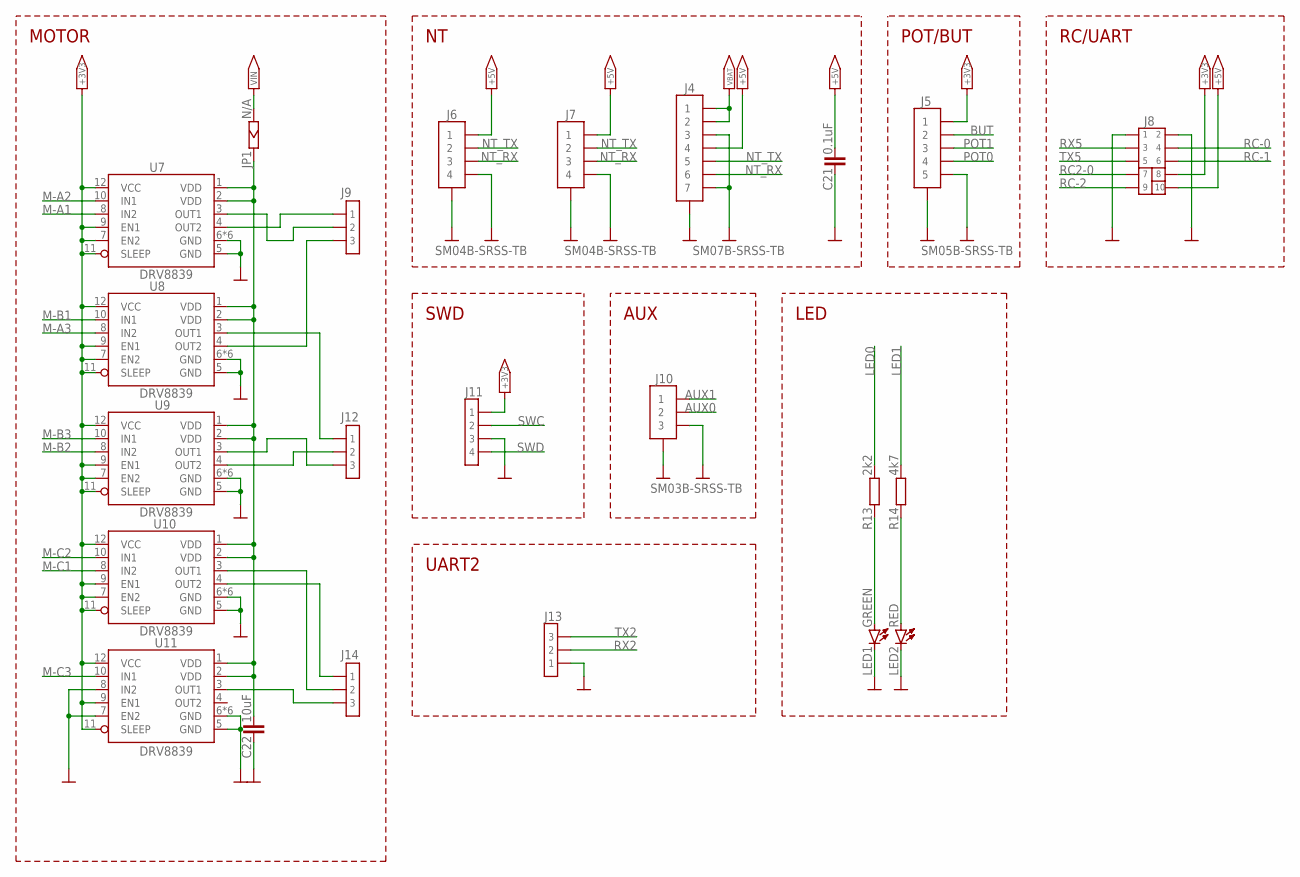
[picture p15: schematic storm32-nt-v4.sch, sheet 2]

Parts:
C21: 0.1uF; 0402[1005-METRIC]
C22: 10uF; 1206[3216-METRIC]; VOLTAGE 63; MOUSER 81-GRM32ER71J106MA2L
J4: SM07B-SRSS-TB
J5: SM05B-SRSS-TB
J6, J7: SM04B-SRSS-TB
J8: HEADER; 2X5
J9, J12, J13, J14: HEADER_THT_2.54X1N_MALE-03-2.54-2.54; HEADER_THT_2.54X1N_MALE-03
J10: SM03B-SRSS-TB
J11: HEADER_THT_1.27X1N_MALE-04-1.27-1.27; HEADER_THT_1.27X1N_MALE-04
JP1: N/A; 0603[1608-METRIC]-0OHM-OFF
LED1: GREEN; 0603[1608-METRIC]-DIODE
LED2: RED; 0603[1608-METRIC]-DIODE
R13: 2k2; 0402[1005-METRIC]
R14: 4k7; 0402[1005-METRIC]
U7, U8, U9, U10, U11: DRV8839; WSON12

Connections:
+3V3: J5.1, J8.8, J11.1, U7.7 (EN2), U7.9 (EN1), U7.11 (SLEEP), U7.12 (VCC), U8.7 (EN2), U8.9 (EN1), U8.11 (SLEEP), U8.12 (VCC), U9.7 (EN2), U9.9 (EN1), U9.11 (SLEEP), U9.12 (VCC), U10.7 (EN2), U10.9 (EN1), U10.11 (SLEEP), U10.12 (VCC), U11.9 (EN1), U11.11 (SLEEP), U11.12 (VCC); also elsewhere on the board
+5V: C21.P$1 (1), J4.4, J6.1, J7.1, J8.10; also elsewhere on the board
AUX0: J10.2; also elsewhere on the board
AUX1: J10.1; also elsewhere on the board
BUT: J5.2; also elsewhere on the board
GND: C21.P$2 (2), C22.P$2 (2), J4.3, J4.7, J4.FIT@1, J4.FIT@2, J5.5, J5.FIT@1, J5.FIT@2, J6.4, J6.FIT@1, J6.FIT@2, J7.4, J7.FIT@1, J7.FIT@2, J8.1, J8.2, J10.3, J10.FIT@1, J10.FIT@2, J11.3, J13.1, LED1.C, LED2.C, U7.5 (GND), U7.6 (GND), U7.GND1 (GND), U7.GND2 (GND), U7.GND3 (GND), U7.GND4 (GND), U7.GND5 (GND), U8.5 (GND), U8.6 (GND), U8.GND1 (GND), U8.GND2 (GND), U8.GND3 (GND), U8.GND4 (GND), U8.GND5 (GND), U9.5 (GND), U9.6 (GND), U9.GND1 (GND), U9.GND2 (GND), U9.GND3 (GND), U9.GND4 (GND), U9.GND5 (GND), U10.5 (GND), U10.6 (GND), U10.GND1 (GND), U10.GND2 (GND), U10.GND3 (GND), U10.GND4 (GND), U10.GND5 (GND), U11.5 (GND), U11.6 (GND), U11.7 (EN2), U11.8 (IN2), U11.GND1 (GND), U11.GND2 (GND), U11.GND3 (GND), U11.GND4 (GND), U11.GND5 (GND); also elsewhere on the board
LED0: R13.P$2; also elsewhere on the board
LED1: R14.P$2; also elsewhere on the board
M-A1: U7.8 (IN2); also elsewhere on the board
M-A2: U7.10 (IN1); also elsewhere on the board
M-A3: U8.8 (IN2); also elsewhere on the board
M-B1: U8.10 (IN1); also elsewhere on the board
M-B2: U9.8 (IN2); also elsewhere on the board
M-B3: U9.10 (IN1); also elsewhere on the board
M-C1: U10.8 (IN2); also elsewhere on the board
M-C2: U10.10 (IN1); also elsewhere on the board
M-C3: U11.10 (IN1); also elsewhere on the board
unnamed: LED1.A, R13.P$1
unnamed: C22.P$1 (1), JP1.P$2, U7.1 (VDD), U7.2 (VDD), U8.1 (VDD), U8.2 (VDD), U9.1 (VDD), U9.2 (VDD), U10.1 (VDD), U10.2 (VDD), U11.1 (VDD), U11.2 (VDD)
unnamed: LED2.A, R14.P$1
unnamed: J9.1, U7.4 (OUT2)
unnamed: J9.2, U7.3 (OUT1)
unnamed: J9.3, U8.4 (OUT2)
unnamed: J12.1, U8.3 (OUT1)
unnamed: J12.2, U9.4 (OUT2)
unnamed: J12.3, U9.3 (OUT1)
unnamed: J14.2, U10.3 (OUT1)
unnamed: J14.1, U10.4 (OUT2)
unnamed: J14.3, U11.3 (OUT1)
NT_RX: J4.6, J6.3, J7.3; also elsewhere on the board
NT_TX: J4.5, J6.2, J7.2; also elsewhere on the board
POT0: J5.4; also elsewhere on the board
POT1: J5.3; also elsewhere on the board
RC2-0: J8.7; also elsewhere on the board
RC-0: J8.4; also elsewhere on the board
RC-1: J8.6; also elsewhere on the board
RC-2: J8.9; also elsewhere on the board
RX2: J13.2; also elsewhere on the board
RX5: J8.3; also elsewhere on the board
SWC: J11.2; also elsewhere on the board
SWD: J11.4; also elsewhere on the board
TX2: J13.3; also elsewhere on the board
TX5: J8.5; also elsewhere on the board
VBAT: J4.1, J4.2; also elsewhere on the board
VIN: JP1.P$1; also elsewhere on the board

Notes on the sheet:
MOTOR
POT/BUT
SWD
AUX
UART2
LED
RC/UART

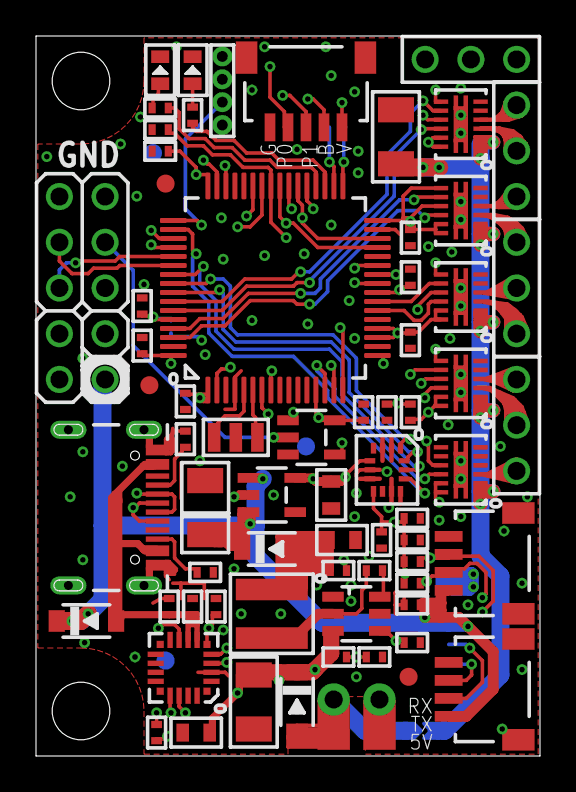
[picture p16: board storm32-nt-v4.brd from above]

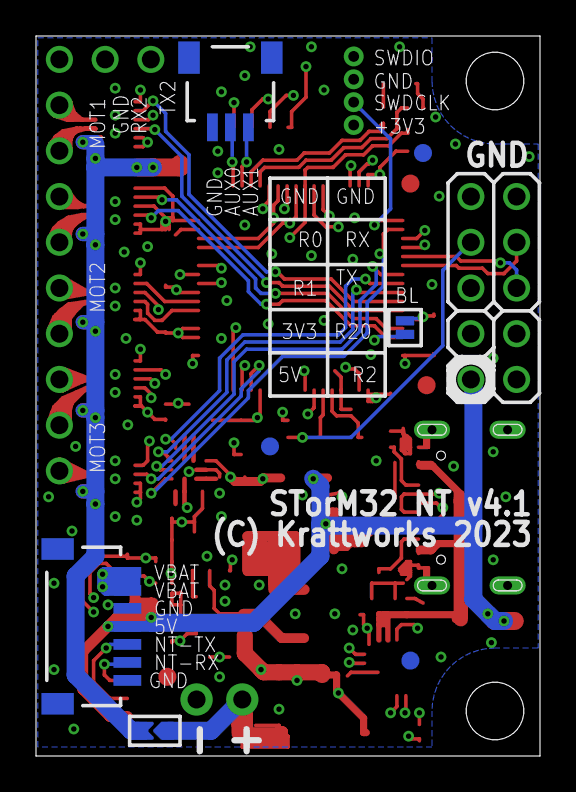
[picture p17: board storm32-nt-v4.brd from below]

Board: 4 copper layers, 28.0 x 40.0 mm, 77 parts (7 on the bottom side), 69 nets.

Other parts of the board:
FRAMEBRD1: A5L-LOC

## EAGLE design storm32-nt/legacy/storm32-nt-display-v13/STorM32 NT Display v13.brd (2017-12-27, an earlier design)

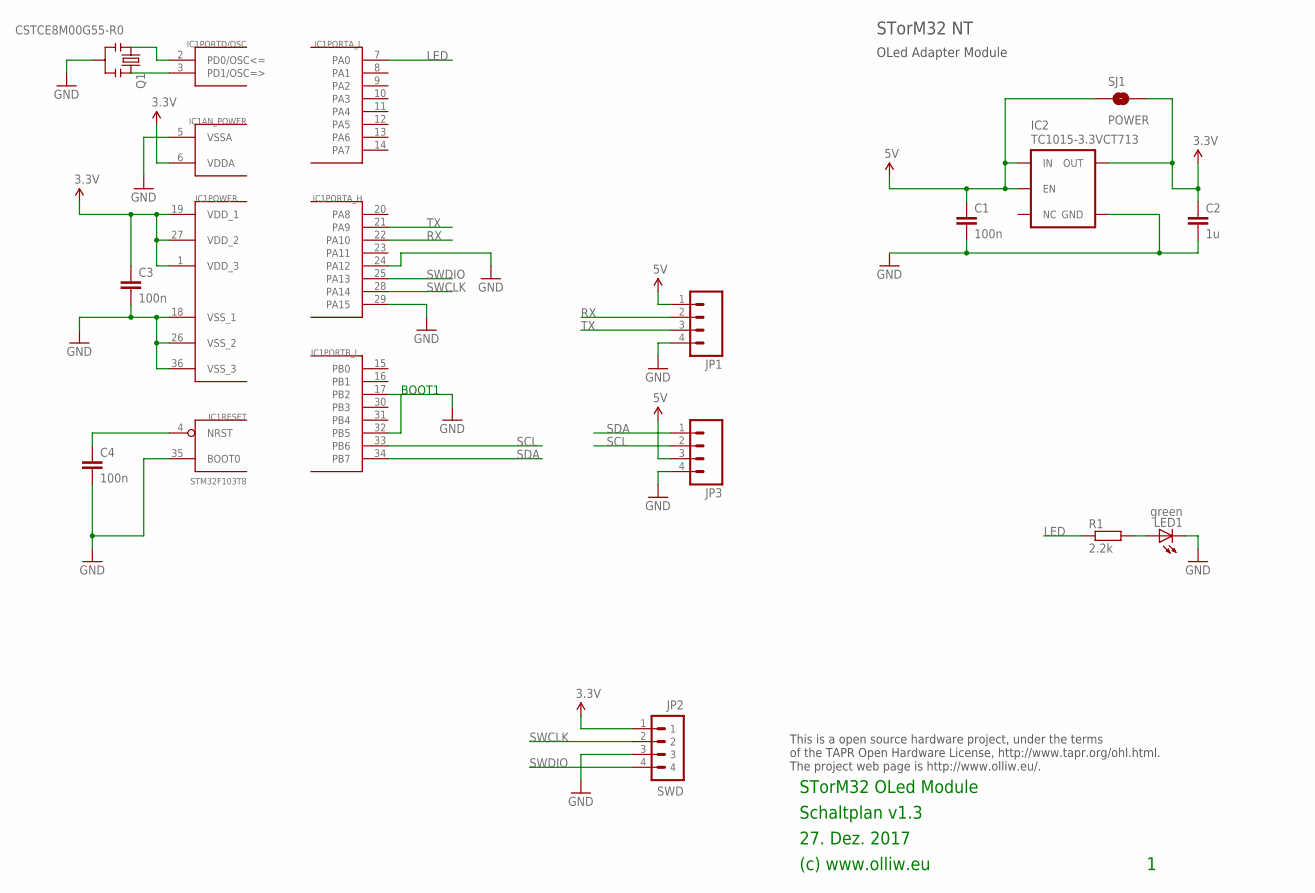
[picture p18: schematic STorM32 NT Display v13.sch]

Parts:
C1, C3, C4: 100n; C0603
C2: 1u; C0603
IC1: STM32F103T8; VFQFPN36
IC2: TC1015-3.3VCT713; SOT23-5
JP1, JP3: M04PTH; 1X04
JP2: SWD; 4X1_1P27_OCT_BILEX
LED1: green; CHIPLED_0603
Q1: CSTCE8M00G55-R0; RESONATOR-SMD
R1: 2.2k; R0603
SJ1: POWER; SJ_2S-NO

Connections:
3.3V: C2.1, C3.1, IC1.1 (VDD_3), IC1.6 (VDDA), IC1.19 (VDD_1), IC1.27 (VDD_2), IC2.5 (OUT), JP2.1, SJ1.2
5V: C1.1, IC2.1 (IN), IC2.3 (EN), JP1.1, JP3.3, SJ1.1
GND: C1.2, C2.2, C3.2, C4.2, IC1.5 (VSSA), IC1.17 (PB2), IC1.18 (VSS_1), IC1.24 (PA12), IC1.26 (VSS_2), IC1.29 (PA15), IC1.32 (PB5), IC1.35 (BOOT0), IC1.36 (VSS_3), IC2.2 (GND), JP1.4, JP2.3, JP3.4, LED1.C, Q1.2
LED: IC1.7 (PA0), R1.1
unnamed: C4.1, IC1.4 (NRST)
unnamed: LED1.A, R1.2
unnamed: IC1.2 (PD0/OSC<=), Q1.1
unnamed: IC1.3 (PD1/OSC=>), Q1.3
RX: IC1.22 (PA10), JP1.2
SCL: IC1.33 (PB6), JP3.2
SDA: IC1.34 (PB7), JP3.1
SWCLK: IC1.28 (PA14), JP2.2
SWDIO: IC1.25 (PA13), JP2.4
TX: IC1.21 (PA9), JP1.3

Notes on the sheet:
27. Dez. 2017
(c) www.olliw.eu
STorM32 OLed Module
Schaltplan v1.3
This is a open source hardware project, under the terms of the TAPR Open Hardware License, http://www.tapr.org/ohl.html. The project web page is http://www.olliw.eu/.
OLed Adapter Module
STorM32 NT
BOOT1

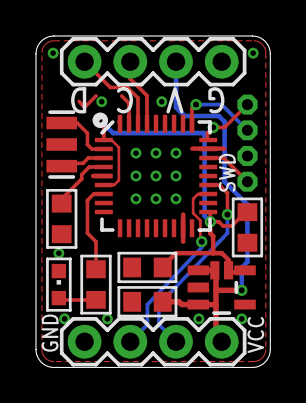
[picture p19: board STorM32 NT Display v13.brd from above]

Board: 2 copper layers, 13.0 x 18.4 mm, 13 parts (0 on the bottom side), 14 nets.

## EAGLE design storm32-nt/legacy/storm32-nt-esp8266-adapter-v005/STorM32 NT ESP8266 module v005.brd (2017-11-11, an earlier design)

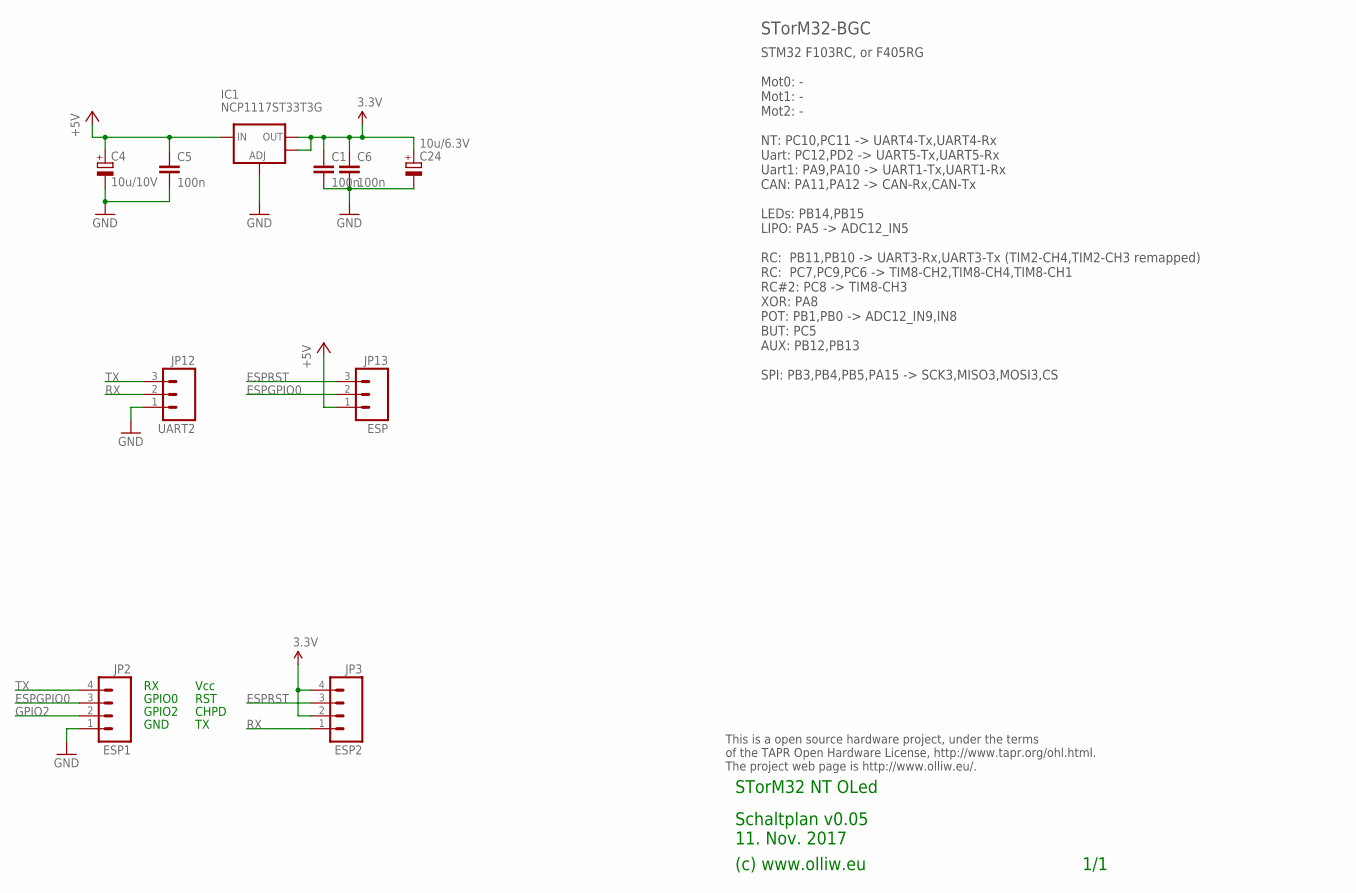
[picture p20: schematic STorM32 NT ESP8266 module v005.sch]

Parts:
C1, C5, C6: 100n; C0603
C4: 10u/10V; SMC_A
C24: 10u/6.3V; SMC_B
IC1: NCP1117ST33T3G; SOT223
JP2: ESP1; 1X04_NO_SILK
JP3: ESP2; 1X04_NO_SILK
JP12: UART2; 1X03_NO_SILK
JP13: ESP; 1X03_NO_SILK

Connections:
3.3V: C1.1, C6.1, C24.+, IC1.2 (OUT), IC1.4 (OUT), JP3.2, JP3.4
+5V: C4.+, C5.1, IC1.3 (IN), JP13.1
ESPGPIO0: JP2.3, JP13.2
ESPRST: JP3.3, JP13.3
GND: C1.2, C4.-, C5.2, C6.2, C24.-, IC1.1 (ADJ), JP2.1, JP12.1
GPIO2: JP2.2
RX: JP3.1, JP12.2
TX: JP2.4, JP12.3

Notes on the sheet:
(c) www.olliw.eu
STorM32 NT OLed
This is a open source hardware project, under the terms of the TAPR Open Hardware License, http://www.tapr.org/ohl.html. The project web page is http://www.olliw.eu/.
STM32 F103RC, or F405RG Mot0: - Mot1: - Mot2: - NT: PC10,PC11 -> UART4-Tx,UART4-Rx Uart: PC12,PD2 -> UART5-Tx,UART5-Rx Uart1: PA9,PA10 -> UART1-Tx,UART1-Rx CAN: PA11,PA12 -> CAN-Rx,CAN-Tx LEDs: PB14,PB15 LIPO: PA5 -> ADC12_IN5 RC: PB11,PB10 -> UART3-Rx,UART3-Tx (TIM2-CH4,TIM2-CH3 remapped) RC: PC7,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
STorM32-BGC
1/1
Schaltplan v0.05 11. Nov. 2017
GPIO0
GPIO2
GND
Vcc
RST
CHPD

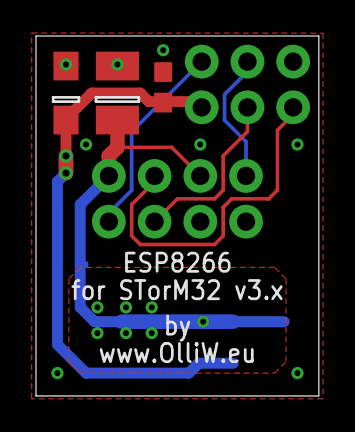
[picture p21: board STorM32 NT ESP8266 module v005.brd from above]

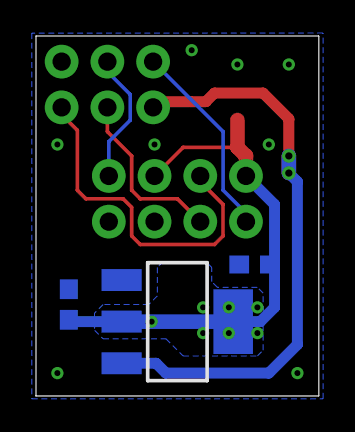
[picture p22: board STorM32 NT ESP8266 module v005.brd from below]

Board: 2 copper layers, 15.7 x 20.0 mm, 10 parts (3 on the bottom side), 7 nets.

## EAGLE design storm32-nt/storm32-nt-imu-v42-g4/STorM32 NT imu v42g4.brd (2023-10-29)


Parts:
C1: 10u/10V; C1206
C2: 1u; C0603
C3, C4, C5, C7: 100n; C0402
C6: 2.2u; C0603
C8, C10: 10n; C0402
C9: 1u; C0402
IC1: STM32G431KB; UFQFPN32
IC2, IC4: LDO-TLV767; WSON-6-2X2
IC3: ICM-42688-P/V; LGA14-2.5X3
JP1: NT; SM04B-SRSS-TB
LED1: red; CHIPLED_0603
LED2: green; CHIPLED_0603
Q1: ECS-TXO-2520MV-240; TXCO-25X20
R1: 10k; R0402
R2: 4.7k; R0402
R3: 2.2k; R0402
SJ1: BOOT0; SJ_2S-NO
SJ2: IMU-ID2; SJ_2S-NO

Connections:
3.3V: C2.1, C4.1, C5.1, C8.1, C10.1, IC1.1 (VDD_1), IC1.15 (VDDA), IC1.17 (VDD_2), IC2.1 (OUT), IC2.2 (SNS), IC3.5 (VDDIO), Q1.4 (VCC), R2.1, SJ1.1
3.3VA: C6.1, C7.1, IC3.8 (VDD), IC4.1 (OUT), IC4.2 (SNS)
5V: C1.1, C9.1, IC2.4 (EN), IC2.6 (IN), IC4.4 (EN), IC4.6 (IN), JP1.1
CS: IC1.9 (PA4), IC3.12 (CS)
EXT0/ADC1: IC1.6 (PA1)
EXT1/T1CH1: IC1.18 (PA8)
EXT2/RX2: IC1.8 (PA3)
EXT3/TX2: IC1.7 (PA2)
FSYNC: IC1.28 (PB5), IC3.9 (FSYNC)
GND: C1.2, C2.2, C3.2, C4.2, C5.2, C6.2, C7.2, C8.2, C9.2, C10.2, IC1.14 (VSSA), IC1.16 (VSS_2), IC1.21 (PA11), IC1.22 (PA12), IC1.30 (PB7), IC1.32 (VSS_1), IC2.3 (GND), IC2.5 (GND), IC2.7 (GND), IC3.2 (RES), IC3.3 (RES), IC3.6 (GND), IC3.7 (RESV), IC3.10 (RES), IC3.11 (RES), IC4.3 (GND), IC4.5 (GND), IC4.7 (GND), JP1.4, LED1.C, LED2.C, Q1.2 (GND), R1.1, SJ2.1
INT: IC1.13 (PB0), IC3.4 (INT)
LED: IC1.26 (JTDO/PB3), R3.1
MISO: IC1.11 (PA6), IC3.1 (SDO/AD0)
MOSI: IC1.12 (PA7), IC3.14 (SDI/SDA)
unnamed: C3.1, IC1.4 (NRST)
unnamed: LED2.A, R3.2
unnamed: IC1.31 (PB8/BOOT0), R1.2, SJ1.2
unnamed: IC1.29 (PB6), SJ2.2
unnamed: LED1.A, R2.2
OSC_IN: IC1.2 (OSC_IN), Q1.3 (OUT)
RX: IC1.20 (PA10), JP1.2
SCK: IC1.10 (PA5), IC3.13 (CLK/SCL)
SWCLK: IC1.24 (PA14/SWCLK)
SWDIO: IC1.23 (PA13/SWDIO)
TX: IC1.19 (PA9), JP1.3

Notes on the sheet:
11. Oct. 2023
(c) www.olliw.eu
STorM32 NT IMU module
Schaltplan v4.2 G4
This is a open source hardware project, under the terms of the TAPR Open Hardware License, http://www.tapr.org/ohl.html. The project web page is http://www.olliw.eu/.
1/1
IMU Module G4, dual LDO, TXCO ICM 42688-P, 42688-V
STorM32 NT
SCK
MISO
MOSI
dummy
T2CH3
RX2
TX2
ICM 42688-P ICM 42688-V
T2CH2
ADC12_IN2
T2CH4
T1CH1
PA0,PA15 are used for RS485 signals


Board: 2 copper layers, 16.5 x 20.5 mm, 23 parts (0 on the bottom side), 19 nets.

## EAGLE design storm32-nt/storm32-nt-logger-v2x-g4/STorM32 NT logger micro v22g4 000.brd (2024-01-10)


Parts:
BAT1: CELL-SMD-6P8; CELL-RECHARGABLE-6P8
C1: 10u/10V; SMC_B
C2, C10: 100n; C0603
C3: 1u; C0603
C4, C5, C6, C7, C8, C9: 100n; C0402
IC1: STM32G431CB; UFQFPN48
IC2: LDO-TLV767; WSON-6-2X2
JP1: NTX; SM04B-SRSS-TB
LED1: red; CHIPLED_0603
LED2, LED3: green; CHIPLED_0603
PH1: SWD; 4X1_1P27_OCT_BILEX
PH2: PINHEAD_5X1WITHOUT; PINHEAD_5X1_WO
Q1: CSTCE8M00G55-R0; RESONATOR-SMD
Q2: ECS-327TXO-2012-33-TR; TXCO-20X12
R1: 4.7k; R0402
R2, R5: 2.2k; R0402
R3, R4: 47k; R0402
U1: 3M 2908-05WB-MG ??; MICROSD

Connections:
3.3V: C3.1, C4.1, C5.1, C6.1, C9.1, IC1.20 (VREF+), IC1.21 (VDDA), IC1.23 (VDD_1), IC1.35 (VDD_2), IC1.48 (VDD_3), IC2.1 (OUT), IC2.2 (SNS), PH1.1, R1.1, R3.2, R4.2, U1.4 (VDD)
5V: C1.+, C2.1, C10.1, IC2.4 (EN), IC2.6 (IN), JP1.1, PH2.2
CD1: IC1.17 (PB0), U1.CD1 (CARD_DETECT), U1.CD2 (CARD_DETECT1)
CS: IC1.12 (PA4), U1.2 (CS)
GND: BAT1.P- (GND), C1.-, C2.2, C3.2, C4.2, C5.2, C6.2, C7.2, C8.2, C9.2, C10.2, IC1.9 (PA1), IC1.11 (PA3), IC1.18 (PB1), IC1.19 (PB2), IC1.26 (PB13), IC1.29 (PC6), IC1.33 (PA11), IC1.34 (PA12), IC1.39 (PC10), IC1.43 (PB5), IC1.46 (PB8/BOOT0), IC2.3 (GND), IC2.5 (GND), IC2.7 (GND), JP1.4, LED1.C, LED2.C, LED3.C, PH1.3, PH2.5, Q1.2, Q2.2 (GND), U1.6 (VSS), U1.MT1 (GND), U1.MT2 (GND1)
LED: IC1.10 (PA2), R2.1, R5.1
unnamed: C7.1, IC1.7 (NRST)
unnamed: LED2.A, R2.2
unnamed: IC1.5 (OSC_IN), Q1.1
unnamed: IC1.6 (OSC_OUT), Q1.3
unnamed: IC1.3 (PC14), Q2.3 (OUT)
unnamed: LED1.A, R1.2
unnamed: LED3.A, R5.2
RX: IC1.32 (PA10), JP1.2, PH2.3
SCK: IC1.13 (PA5), U1.5 (SCLK)
SDI: IC1.15 (PA7), U1.3 (DATA_IN)
SDO: IC1.14 (PA6), R4.1, U1.7 (DATA_OUT)
SWCLK: IC1.37 (PA14/SWCLK), PH1.2
SWDIO: IC1.36 (PA13/SWDIO), PH1.4
TX: IC1.31 (PA9), JP1.3, PH2.4, R3.1
VBAT: BAT1.P+ (BAT+), C8.1, IC1.1 (VBAT), Q2.4 (VCC)
VCC: PH2.1

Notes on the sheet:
30. Oct. 2023
(c) www.olliw.eu
STorM32 NT Logger Module
Schaltplan v2.2 rev00
This is a open source hardware project, under the terms of the TAPR Open Hardware License, http://www.tapr.org/ohl.html. The project web page is http://www.olliw.eu/.
1/1
Logger Module
STorM32 NT
SCK
MISO
MOSI
BOOT1
dummy
3M Electronics: 2908-05WB-MG ?
NT-RX
NT-TX
v2.1: - TXCO instead of XCO v2.2: - TXCO 2.0x1.2 mm - bat package changed



Board: 2 copper layers, 26.0 x 26.0 mm, 27 parts (3 on the bottom side), 21 nets.

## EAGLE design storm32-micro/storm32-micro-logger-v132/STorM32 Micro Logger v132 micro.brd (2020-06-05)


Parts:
C1: 10u/10V; SMC_B
C2, C9: 100n; C0603
C3: 1u; C0603
C4, C5, C6, C7, C8, C10: 100n; C0402
IC1: STM32F103T8; VFQFPN36
IC2: TC1015-3.3VCT713; SOT23-5
IC3: DS3231M; SO08
JP1: PINHEAD_5X1WITHOUT; PINHEAD_5X1_WO
LED1: red; CHIPLED_0603
LED2: green; CHIPLED_0603
NTX: NTX; SM04B-SRSS-TB
PH1: SWD; 4X1_1P27_OCT_BILEX
Q1: CSTCE8M00G55-R0; RESONATOR-SMD
R1: 4.7k; R0402
R2: 2.2k; R0402
R3, R4: 47k; R0402
R5, R6: 1k; R0402
U1: 3M 2908-05WB-MG ??; MICROSD
U$1: CELLCLIP10MM; CELLCLIP-10MM

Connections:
3.3V: C3.1, C4.1, C5.1, C6.1, C8.1, C10.1, IC1.1 (VDD_3), IC1.6 (VDDA), IC1.19 (VDD_1), IC1.27 (VDD_2), IC2.5 (OUT), IC3.2 (VCC), PH1.1, R1.1, R3.2, R4.2, R5.2, R6.2, U1.4 (VDD)
5V: C1.+, C2.1, C9.1, IC2.1 (IN), IC2.3 (EN), JP1.2, NTX.1
BAT+: IC3.6 (VBAT), U$1.P$2 (BAT+)
CD1: IC1.15 (PB0), U1.CD1 (CARD_DETECT), U1.CD2 (CARD_DETECT1)
CS: IC1.11 (PA4), U1.2 (CS)
GND: C1.-, C2.2, C3.2, C4.2, C5.2, C6.2, C7.2, C8.2, C9.2, C10.2, IC1.5 (VSSA), IC1.17 (PB2), IC1.18 (VSS_1), IC1.23 (PA11), IC1.26 (VSS_2), IC1.32 (PB5), IC1.35 (BOOT0), IC1.36 (VSS_3), IC2.2 (GND), IC3.5 (GND), JP1.5, LED1.C, LED2.C, NTX.4, PH1.3, Q1.2, U1.6 (VSS), U1.MT1 (GND), U1.MT2 (GND1), U$1.P$1 (GND)
LED: IC1.9 (PA2), R2.1
unnamed: C7.1, IC1.4 (NRST)
unnamed: LED2.A, R2.2
unnamed: IC1.2 (PD0/OSC<=), Q1.1
unnamed: IC1.3 (PD1/OSC=>), Q1.3
unnamed: LED1.A, R1.2
RX: IC1.22 (PA10), JP1.3, NTX.2
SCK: IC1.12 (PA5), U1.5 (SCLK)
SCL: IC1.33 (PB6), IC3.8 (SCL), R5.1
SDA: IC1.34 (PB7), IC3.7 (SDA), R6.1
SDI: IC1.14 (PA7), U1.3 (DATA_IN)
SDO: IC1.13 (PA6), R4.1, U1.7 (DATA_OUT)
SWCLK: IC1.28 (PA14), PH1.2
SWDIO: IC1.25 (PA13), PH1.4
TX: IC1.10 (PA3), IC1.21 (PA9), JP1.4, NTX.3, R3.1
VCC: JP1.1

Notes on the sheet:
26. Mai 2020
(c) www.olliw.eu
STorM32 NT Logger Module
Schaltplan v1.32
This is a open source hardware project, under the terms of the TAPR Open Hardware License, http://www.tapr.org/ohl.html. The project web page is http://www.olliw.eu/.
1/1
Logger Module
STorM32 NT
SCK
MISO
MOSI
BOOT1
dummy
3M Electronics: 2908-05WB-MG ?
NT-RX
NT-TX



Board: 2 copper layers, 26.0 x 26.0 mm, 27 parts (11 on the bottom side), 21 nets.

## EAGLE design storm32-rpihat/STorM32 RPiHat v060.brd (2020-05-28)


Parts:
3.3V1, 3.3V2, 5V, 5V1: TPB1,27; B1,27
5VSEL: SJ-2WAY-WCREAM; SJ-2WAY-BIG-WCREAM
AUX0, AUX1: TPB1,27; B1,27
BL: BOOT0; SJ_2S-NO
BUT: TPB1,27; B1,27
C1: 10n; C0402
C2, C6, C8, C9, C10, C11, C12, C13, C14, C15, C17, C20: 100n; C0402
C3: 2.2u; C0603
C4: 10u/10V; SMC_A
C5, C16: 100n; C0603
C7: 10u/6.3V; SMC_A
C18: 22p; C0402
C19: 33p; C0402
ESPGPIO: TPB1,27; B1,27
ESPRST: TPB1,27; B1,27
IC1: STM32F103RCT6; TQFP64
IC2: TC1185-3.3VCT713; SOT23-5
IC3: 74AHC1G86; SOT23-5-VER1
IC4: ICM42605; LGA14-2.5X3
IC5: CAT24C32; TSSOP8-4.3X3
IC6: SC16IS762; QFN-32
JP1: NT-X; SM06B-SRSS-TB
JP2: NT; SM04B-SRSS-TB
JP3, JP4: JST-GH-6SIDE-ENTRY; SM06B-GHS-TB
LED1: green; CHIPLED_0603
LED2: red; CHIPLED_0603
LED3: orange; CHIPLED_0603
PH1: SWD; 4X1_1P27_OCT_BILEX
PH2: PINHEAD_5X1WITHOUT; PINHEAD_5X1_WO
PH3: RPI-UHAT; RPI-40W-UHAT
PH4: PINHEAD_3X1WITHBORDER; PINHEAD_3X1
POT0, POT1: TPB1,27; B1,27
Q1: CSTCE8M00G55-R0; RESONATOR-SMD
Q2: ECS-147.4-12-33-AG; CRYSTAL-SMD-3P2X2P5
R1, R6, R12: 10k; R0402
R2: 4.7k; R0402
R3, R4, R5: 2.2k; R0402
R7: 15k; R0402
R8: 1.5k; R0402
R9, R10: 3.9k; R0402
R11, R13, R14: 1k; R0402
RC0, RC1, RC2: TPB1,27; B1,27
RX1, RX2: TPB1,27; B1,27
TX1, TX2: TPB1,27; B1,27
VBAT: TPB1,27; B1,27
WP: SJ-2WAY-WCREAM; SJ-2WAY-BIG-WCREAM

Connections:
3.3V: 3.3V1.TP, 3.3V2.TP, BL.2, C1.1, C2.1, C3.1, C6.1, C7.+, C8.1, C9.1, C10.1, C11.1, IC1.1 (VBAT), IC1.13 (VDDA), IC1.19 (VDD_4), IC1.20 (PA4), IC1.32 (VDD_1), IC1.48 (VDD_2), IC1.64 (VDD_3), IC2.5 (OUT), IC3.5 (VCC), IC4.5 (VDDIO), IC4.8 (VDD), PH1.1, R4.2, R5.2
+5V: 5V.TP, 5V1.TP, 5VSEL.1, C4.+, C5.1, C14.1, C15.1, IC2.1 (IN), IC2.3 (EN), JP1.3, JP2.1, PH2.2
AUX0: AUX0.TP, IC1.33 (PB12)
AUX1: AUX1.TP, IC1.34 (PB13)
BOOT0: BL.1, IC1.60 (BOOT0), R1.1
BUT: BUT.TP, IC1.25 (PC5)
CANRX: IC1.44 (PA11)
CANTX: IC1.45 (PA12)
CS: IC1.50 (PA15), IC1.59 (PB7), IC4.12 (CS)
CS_RPI: IC1.62 (PB9), PH3.36 (GPIO16)
CTSB: IC6.15 (CTSB), JP3.4
ESPGPIO0: ESPGPIO.TP, IC1.15 (PA1)
ESPRST: ESPRST.TP, IC1.14 (PA0)
GND: C1.2, C2.2, C3.2, C4.-, C5.2, C6.2, C7.-, C8.2, C9.2, C10.2, C11.2, C12.2, C13.2, C14.2, C15.2, C16.2, C17.2, C18.1, C19.1, C20.2, IC1.4 (PC15), IC1.9 (PC1), IC1.10 (PC2), IC1.12 (VSSA), IC1.18 (VSS_4), IC1.22 (PA6), IC1.28 (PB2), IC1.31 (VSS_1), IC1.47 (VSS_2), IC1.58 (PB6), IC1.63 (VSS_3), IC2.2 (GND), IC3.3 (GND), IC4.2 (RES), IC4.3 (RES), IC4.6 (GND), IC4.7 (RESV), IC4.9 (FSYNC), IC4.10 (RES), IC4.11 (RES), IC5.1 (A0), IC5.2 (A1), IC5.3 (A2), IC5.4 (GND), IC6.6 (I2C/SPI), IC6.11 (SDA), IC6.12 (GND), IC6.21 (GND), IC6.29 (GND), JP1.2, JP1.6, JP2.4, JP3.6, JP4.6, LED1.C, LED2.C, LED3.C, PH1.3, PH2.5, PH3.6 (GND), PH3.9 (GND), PH3.14 (GND), PH3.20 (GND), PH3.25 (GND), PH3.30 (GND), PH3.34 (GND), PH3.39 (GND), PH4.1, Q1.2, R1.2, R6.1, R8.1, WP.1
ID_SC: IC5.6 (SCL), PH3.28 (ID_SC), R9.1
ID_SD: IC5.5 (SDA), PH3.27 (ID_SD), R10.1
INT: IC4.4 (INT)
LED0: IC1.35 (PB14), R3.1
LED1: IC1.36 (PB15), R2.1
LIPO: C13.1, IC1.24 (PC4), R7.2, R8.2
MISO3: IC1.56 (PB4), IC4.1 (SDO/AD0), PH3.35 (GPIO19)
MOSI3: IC1.57 (PB5), IC4.14 (SDI/SDA), PH3.38 (GPIO20)
unnamed: IC6.2 (RESET), R12.1
unnamed: C18.2, IC6.3 (XTAL1), Q2.3 (2)
unnamed: C19.2, IC6.4 (XTAL2), Q2.1
unnamed: LED1.A, R3.2
unnamed: LED2.A, R2.2
unnamed: LED3.A, R14.1
unnamed: IC1.5 (PD0/OSC<=), Q1.3
unnamed: IC1.6 (PD1/OSC=>), Q1.1
unnamed: IC5.7 (WP), R11.1, WP.2
NRST: C12.1, IC1.7 (NRST), PH3.31 (GPIO6)
NT-RX: IC1.52 (PC11), JP1.5, JP2.3, PH2.4, R4.1
NT-TX: IC1.51 (PC10), JP1.4, JP2.2, PH2.3, R5.1
PC0: IC1.8 (PC0), PH3.29 (GPIO5)
POT0: IC1.27 (PB1), POT0.TP
POT1: IC1.26 (PB0), POT1.TP
RC0-IN: IC3.2 (I1), RC0.TP
RC0/RX3: IC1.30 (PB11), IC1.38 (PC7), IC3.4 (O)
RC1/TX3: IC1.29 (PB10), IC1.40 (PC9), RC1.TP
RC2: IC1.37 (PC6), RC2.TP
RC2-0: IC1.39 (PC8)
RPI3.3V: C17.1, C20.1, IC5.8 (VCC), IC6.5 (VDD), IC6.13 (VDD), IC6.28 (VDD), PH3.1 (3.3V), R9.2, R10.2, R11.2, R12.2, R13.2
RPI5V: 5VSEL.2, JP3.1, JP4.1, PH3.2 (5.0V), PH3.4 (5.0V)
RPI-RXD: JP4.3, PH3.10 (RXD)
RPI-TXD: JP4.2, PH3.8 (TXD)
RPI_CLK: IC6.10 (SCL), PH3.23 (SPI_SCLK)
RPI_CS: IC6.7 (CS/A0), PH3.24 (SPI_CE0)
RPI_INT: IC6.14 (IRQ), PH3.13 (GPIO27), R13.1
RPI_LED: PH3.16 (GPIO23), R14.2
RPI_MISO: IC6.9 (SO), PH3.21 (SPI_MISO)
RPI_MOSI: IC6.8 (SI/A1), PH3.19 (SPI_MOSI)
RPI_SCL: JP4.4, PH3.5 (SCL)
RPI_SDA: JP4.5, PH3.3 (SDA)
RTSB: IC6.16 (RTSB), JP3.5
RX1: IC1.43 (PA10), RX1.TP
RX2: IC1.17 (PA3), RX2.TP
RX5: IC1.54 (PD2), IC6.32 (TXA), PH4.2 (3)
RXB: IC6.23 (RXB), JP3.3
SCK3: IC1.55 (PB3), IC4.13 (CLK/SCL), PH3.40 (GPIO21)
SWCLK: IC1.49 (PA14), PH1.2
SWDIO: IC1.46 (PA13), PH1.4
TX1: IC1.42 (PA9), TX1.TP
TX2: IC1.16 (PA2), TX2.TP
TX5: IC1.53 (PC12), IC6.1 (RXA), PH4.3 (5)
TXB: IC6.22 (TXB), JP3.2
VCC: C16.1, JP1.1, PH2.1, R7.1, VBAT.TP
XOR: IC1.41 (PA8), IC3.1 (I0), R6.2

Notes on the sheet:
(c) www.olliw.eu
STorM32 NT BGC
This is a open source hardware project, under the terms of the TAPR Open Hardware License, http://www.tapr.org/ohl.html. The project web page is http://www.olliw.eu/.
STM32 F103RC,F103RE Mot0,1,2: - NT: PC10,PC11 -> UART4-Tx,UART4-Rx Uart: PC12,PD2 -> UART5-Tx,UART5-Rx Uart1: PA9,PA10 -> UART1-Tx,UART1-Rx CAN: PA11,PA12 -> CAN-Rx,CAN-Tx LEDs: PB14,PB15 LIPO: PC4 -> ADC12_IN14 RC: PB11,PB10 -> UART3-Rx,UART3-Tx RC: PC7,PC9,PC6 -> TIM8-CH2,TIM8-CH4,TIM8-CH1 RC#2: 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
RPi uHat v3.3i 26. Mai. 2020
STM32F103RC
STorM32-BGC
1/2
2/2
IC1
ATTENTION: The sequence of the NT Tx,Rx pins is swapped here in comparison to the sequence on the modules
BOOT1
dummy
RPi uHat v3.3i rev006 26. Mai. 2020
PC0-PC3 do not use (board id)
for ShenZhen2U: - JP9 NT-X 6-pin instead of 7-pin - C2: 1u/25V instead of 2.2u - C15: 10V is sufficient, X5R is OK - D5,D6: BAT54J instead of 1PS76SB40 use _2layer_EagleRules.dru with these changes: - Clearance,Sizes: 7mil to 6mil - Distance: Copper/dimension to 15mil - Shapes/Roundness: 5mil, 10%,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
Changes for Micro v3.31: - SPI CS: PA15 and PB7 connected to resolve wiring
used by v1.3 for ADC
used by v1.3 for MOT
not used
used by v1.3 for I2C-CLK
v1.3: - - - - v3.3: - - - - hat: g 0 0 -
Changes for RPi uHat v3.3: - C15, C16 added - PC0-PC3: board id - NRST connected to BCM6 - led3 connected to BCM23 - PC0: connected to BCM5, isr for spi - spi connected to RPI spi1, ce2



Board: 2 copper layers, 65.0 x 30.0 mm, 75 parts (31 on the bottom side), 64 nets.

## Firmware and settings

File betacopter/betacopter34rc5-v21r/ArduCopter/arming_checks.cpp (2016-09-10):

/// -*- tab-width: 4; Mode: C++; c-basic-offset: 4; indent-tabs-mode: nil -*-

#include "Copter.h"

// performs pre-arm checks. expects to be called at 1hz.
void Copter::update_arming_checks(void)
{
    // perform pre-arm checks & display failures every 30 seconds
    static uint8_t pre_arm_display_counter = PREARM_DISPLAY_PERIOD/2;
    pre_arm_display_counter++;
    bool display_fail = false;
    if (pre_arm_display_counter >= PREARM_DISPLAY_PERIOD) {
        display_fail = true;
        pre_arm_display_counter = 0;
    }

    if (pre_arm_checks(display_fail)) {
        set_pre_arm_check(true);
    }
}

// performs pre-arm checks and arming checks
bool Copter::all_arming_checks_passing(bool arming_from_gcs)
{
    if (pre_arm_checks(true)) {
        set_pre_arm_check(true);
    } else {
        return false;
    }

    return ap.pre_arm_check && arm_checks(true, arming_from_gcs);
}

// perform pre-arm checks and set ap.pre_arm_check flag
//  return true if the checks pass successfully
bool Copter::pre_arm_checks(bool display_failure)
{
    // exit immediately if already armed
    if (motors.armed()) {
        return true;
    }

    // check if motor interlock and Emergency Stop aux switches are used
    // at the same time.  This cannot be allowed.
    if (check_if_auxsw_mode_used(AUXSW_MOTOR_INTERLOCK) && check_if_auxsw_mode_used(AUXSW_MOTOR_ESTOP)){
        if (display_failure) {
            gcs_send_text(MAV_SEVERITY_CRITICAL,"PreArm: Interlock/E-Stop Conflict");
        }
        return false;
    }

    // check if motor interlock aux switch is in use
    // if it is, switch needs to be in disabled position to arm
    // otherwise exit immediately.  This check to be repeated,
    // as state can change at any time.
    if (ap.using_interlock && ap.motor_interlock_switch) {
        if (display_failure) {
            gcs_send_text(MAV_SEVERITY_CRITICAL,"PreArm: Motor Interlock Enabled");
        }
        return false;
    }

    // exit immediately if we've already successfully performed the pre-arm check
    if (ap.pre_arm_check) {
        // run gps checks because results may change and affect LED colour
        // no need to display failures because arm_checks will do that if the pilot tries to arm
        pre_arm_gps_checks(false);
        return true;
    }

    // succeed if pre arm checks are disabled
    if (g.arming_check == ARMING_CHECK_NONE) {
//OW
        // do the component prearm check at the very last, we thus may have to bypass this if
        if (!BP_Component_pre_arm_check(display_failure)) return false;
//OWEND
        set_pre_arm_check(true);
        set_pre_arm_rc_check(true);
        return true;
    }

    bool ret = true;
    ret &= barometer_checks(display_failure);
    ret &= rc_calibration_checks(display_failure);
    ret &= compass_checks(display_failure);
    ret &= gps_checks(display_failure);
    ret &= fence_checks(display_failure);
    ret &= ins_checks(display_failure);
    ret &= board_voltage_checks(display_failure);
    ret &= parameter_checks(display_failure);
    ret &= pilot_throttle_checks(display_failure);

//OW
    if (!BP_Component_pre_arm_check(display_failure)) return false;
//OWEND

    return ret;
}

bool Copter::rc_calibration_checks(bool display_failure)
{
    // pre-arm rc checks a prerequisite
    pre_arm_rc_checks();
    if (!ap.pre_arm_rc_check) {
        if (display_failure) {
            gcs_send_text(MAV_SEVERITY_CRITICAL,"PreArm: RC not calibrated");
        }
        return false;
    }
    return true;
}

bool Copter::barometer_checks(bool display_failure)
{
    // check Baro
    if ((g.arming_check == ARMING_CHECK_ALL) || (g.arming_check & ARMING_CHECK_BARO)) {
        // barometer health check
        if (!barometer.all_healthy()) {
            if (display_failure) {
                gcs_send_text(MAV_SEVERITY_CRITICAL,"PreArm: Barometer not healthy");
            }
            return false;
        }
        // Check baro & inav alt are within 1m if EKF is operating in an absolute position mode.
        // Do not check if intending to operate in a ground relative height mode as EKF will output a ground relative height
        // that may differ from the baro height due to baro drift.
        nav_filter_status filt_status = inertial_nav.get_filter_status();
        bool using_baro_ref = (!filt_status.flags.pred_horiz_pos_rel && filt_status.flags.pred_horiz_pos_abs);
        if (using_baro_ref) {
            if (fabsf(inertial_nav.get_altitude() - baro_alt) > PREARM_MAX_ALT_DISPARITY_CM) {
                if (display_failure) {
                    gcs_send_text(MAV_SEVERITY_CRITICAL,"PreArm: Altitude disparity");
                }
                return false;
            }
        }
    }
    return true;
}

bool Copter::compass_checks(bool display_failure)
{
    // check Compass
    if ((g.arming_check == ARMING_CHECK_ALL) || (g.arming_check & ARMING_CHECK_COMPASS)) {
        //check if compass has calibrated and requires reboot
        if (compass.compass_cal_requires_reboot()) {
            if (display_failure) {
                gcs_send_text(MAV_SEVERITY_CRITICAL, "PreArm: Compass calibrated requires reboot");
            }
            return false;
        }

        // check the primary compass is healthy
        if (!compass.healthy()) {
            if (display_failure) {
                gcs_send_text(MAV_SEVERITY_CRITICAL,"PreArm: Compass not healthy");
            }
            return false;
        }

        // check compass learning is on or offsets have been set
        if (!compass.configured()) {
            if (display_failure) {
                gcs_send_text(MAV_SEVERITY_CRITICAL,"PreArm: Compass not calibrated");
            }
            return false;
        }

        // check for unreasonable compass offsets
        Vector3f offsets = compass.get_offsets();
        if (offsets.length() > COMPASS_OFFSETS_MAX) {
            if (display_failure) {
                gcs_send_text(MAV_SEVERITY_CRITICAL,"PreArm: Compass offsets too high");
            }
            return false;
        }

        // check for unreasonable mag field length
        float mag_field = compass.get_field().length();
        if (mag_field > COMPASS_MAGFIELD_EXPECTED*1.65f || mag_field < COMPASS_MAGFIELD_EXPECTED*0.35f) {
            if (display_failure) {
                gcs_send_text(MAV_SEVERITY_CRITICAL,"PreArm: Check mag field");
            }
            return false;
        }

        // check all compasses point in roughly same direction
        if (!compass.consistent()) {
            if (display_failure) {
                gcs_send_text(MAV_SEVERITY_CRITICAL,"PreArm: inconsistent compasses");
            }
            return false;
        }

    }

    return true;
}

bool Copter::gps_checks(bool display_failure)
{
    // check GPS
    if (!pre_arm_gps_checks(display_failure)) {
        return false;
    }
    return true;
}
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

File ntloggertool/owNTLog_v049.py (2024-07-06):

#!/usr/bin/env python
#*******************************************************
# Copyright (c) OlliW42, STorM32 project
# GPL3
# https://www.gnu.org/licenses/gpl-3.0.de.html
# OlliW @ www.olliw.eu
#*******************************************************
# Version v0.49 30. July 2022

###############################################################################
# cNTLogDataItemList
# class to store nt data columns
#-----------------------------------------------------------------------------#
# is needed here since cNTLogFileReader needs a list to generate the header in the datalog

###############################################################################
# cNTLogDataFrame
# this is the class to handle and host the data of one frame
#-----------------------------------------------------------------------------#

#this is a base class for handling NT log data
#class cNTLogDataFrameBase:

#this is a child class for handling NT log data
#class cNTLogDataFrame(cNTLogDataFrameBase):

#this is a child class for handling NT serial data streams
#class cNTLogSerialDataFrame(cNTLogDataFrame):

###############################################################################
# cNTLogParser
# this is the main class to parse a stream of log packets into a cNTLogDataFrame
#-----------------------------------------------------------------------------#

###############################################################################
# cNTLogFileReader
# this is the main class to read in a NTLogger data log file
# it generates a number of data lists, for easier handling in the GUI
#-----------------------------------------------------------------------------#


import struct
from datetime import datetime
from math import sqrt, sin, cos, pi, atan2
from PyQt5.QtCore import QFile
from owNTLoggerObjects_v042 import * #cLogDataItemList


##defined alreadycNTLOGVERSION_UNINITIALIZED = 0
cLOGVERSION_NT_V2 = 2 #new V2 commands
cLOGVERSION_NT_V3 = 3 #SetLog extended to 0.001?
cLOGVERSION_NT_LATEST = 3 #this is an alias to the latest version

#!!!!! IT WILL CRASH IF VERSION IS NOT V3 !!!!!

###############################################################################
# cNTLogDataItemList
# class to store nt data columns
#-----------------------------------------------------------------------------#
# is needed here since cNTLogFileReader needs a list to generate the header in the datalog
# the list must be compatible in sequence to the list used by cLogItemList in the main
class cNTLogDataItemList(cLogDataItemList):

    #this is a human-readable list of how to organize the standard NTLogger data field names into catagories
    #is used in getGraphSelectorList()

    def __init__(self,_translator=None):
        super().__init__(_translator)
        self.setToStandardNTLoggerItemList()
        self.setToStandardNTLoggerGraphSelectorList()

    #the order of the main items can be as we want it to be
    #the order of the sub items within a main item is given by the order in setToStandardNTLoggerItemList()
    def setToStandardNTLoggerGraphSelectorList(self):
        self.graphSelectorList = [
        ['Performance',["Imu1rx","Imu1done","PIDdone","Motdone","Imu2rx","Imu2done","Logdone","Loopdone"]],
        ['Imu1 Pitch,Roll,Yaw',["Imu1Pitch","Imu1Roll","Imu1Yaw"]],
        ['Imu2 Pitch,Roll,Yaw',["Imu2Pitch","Imu2Roll","Imu2Yaw"]],
        ['Encoder Pitch,Roll,Yaw',["EncPitch*","EncRoll*","EncYaw*"]], #injected, converted to angles
        ['PID Error Pitch,Roll,Yaw',["PIDErrorPitch","PIDErrorRoll","PIDErrorYaw"]],
        ['PID SetP Pitch,Roll,Yaw',["PIDEffSetPointPitch*","PIDEffSetPointRoll*","PIDEffSetPointYaw*", #injected
                                    "PIDSetPointPitch","PIDSetPointRoll","PIDSetPointYaw",
                                    "PIDPanSetPointPitch*","PIDPanSetPointRoll*","PIDPanSetPointYaw*"]], #injected
        ['PID P I D Pitch,Roll,Yaw',["PPitch*","PRoll*","PYaw*", #injected
                                     "IPitch","IRoll","IYaw",
                                     "DPitch","DRoll","DYaw",
                                     "IPitch*","IRoll*","IYaw*", #injected
                                     "DPitch*","DRoll*","DYaw*"]], #injected
#        ['PID Pitch,Roll,Yaw',["PIDPitch","PIDRoll","PIDYaw"]],
#        ['PID Mot Pitch,Roll,Yaw',["PIDMotPitch","PIDMotRoll","PIDMotYaw"]],
        ['PID Pitch,Roll,Yaw',["PIDPitch","PIDRoll","PIDYaw","PIDMotPitch","PIDMotRoll","PIDMotYaw"]],
        ['Ahrs1',["Rx1","Ry1","Rz1","AccAmp1*","AccConf1","YawTarget"]],  #AccAmp1 is injected
#        ['State',['State','Status','Status2','ErrorCnt']],
        ['State',['State']],
        ['Error',['ErrorCnt']],
        ['Voltage',['Voltage']],
        ['STorM32 Link',["q0","q1","q2","q3","vx","vy","vz","YawRateCmd","FCStatus","SLStatus",
                         "FailsafeCnt","A1ValidFailCnt","received"]], #STL
        ['Acc1',["ax1","ay1","az1"]],
        ['Gyro1',["gx1","gy1","gz1"]],
        ['Acc2',["ax2","ay2","az2"]],
        ['Gyro2',["gx2","gy2","gz2"]],
        ['Sensor States',["Imu1State","Imu2State","MotState"]],
        ['Acc1 raw',["ax1raw","ay1raw","az1raw"]],
        ['Gyro1 raw',["gx1raw","gy1raw","gz1raw"]],
        ['Acc2 raw',["ax2raw","ay2raw","az2raw"]],
        ['Gyro2 raw',["gx2raw","gy2raw","gz2raw"]],
        ['Temp 1+2',["T1","T2"]],
        ['Mot Flags',["MotFlags"]],
        ['Mot Pitch,Roll,Yaw',["MotPitch","MotRoll","MotYaw"]],
        ['Vmax Pitch,Roll,Yaw',["VmaxPitch","VmaxRoll","VmaxYaw"]],
        ['dU Pitch,Roll,Yaw',["dUPitch*","dURoll*","dUYaw*"]], #injected, converted to angles
        ['Encoder raw',["EncRawPitch","EncRawRoll","EncRawYaw"]],
        ['dU raw',["dURawPitch","dURawRoll","dURawYaw"]],
        ['Inputs',['InputPitch','InputRoll','InputYaw','InputPanMode','InputStandBy','InputCamera',
                   'InputReCenterCamera','InputScript1','InputScript2','InputScript3','InputScript4',
                   'InputPwmOut','InputCamera2']],
        ['Camera',["CameraModel","CameraCmd","CameraValue","CameraPwm","CameraCmd2","CameraValue2"]],
        ['Debug',["debug1","debug2","debug3","debug4","debug5","debug6","debug7","inj1*","inj2*","inj3*"]], #STL
        ]
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

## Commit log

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2014-02-22 folders restructured
    [STorM32 BGC mpu module v008.brd, STorM32 BGC mpu module v008.sch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]
2014-03-11 v1.2 rev2
    [STorM32 BGC mpu module v008.brd, STorM32 BGC mpu module v008.sch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]
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2014-03-21 v1.3 released
    [STorM32 BGC mpu module v008.brd, STorM32 BGC mpu module v008.sch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]
2014-05-06 mpu module v009 eagle files added
    [STorM32 BGC mpu module v008.brd, STorM32 BGC mpu module v008.sch, STorM32 BGC mpu module v009 pannelized2.brd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]
2015-06-15 storm32-nt motor&mpu module files uploaded
    [STorM32 BGC mpu module v008.brd, STorM32 BGC mpu module v008.sch, STorM32 BGC mpu module v009 pannelized2.brd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]
2015-06-30 nt motor module initial release
    [STorM32 NT motor module v008-panelized.GBL, STorM32 NT motor module v008-panelized.GBO, STorM32 NT motor module v008-panelized.GBP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]
2015-07-10 release nt imu modules
    [STorM32 NT imu module v008 mini.GBL, STorM32 NT imu module v008 mini.GBO, STorM32 NT imu module v008 mini.GBP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]
2015-07-16 nt modules upgrade to v1.0
    [STorM32 NT imu module v008 mini.GBL, STorM32 NT imu module v008 mini.GBO, STorM32 NT imu module v008 mini.GBP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]
2015-07-16 nt modules updgrade to v1.0
    [STorM32 NT imu v10 mini-mpu6000.brd, STorM32 NT imu v10 mini-mpu6000.sch, STorM32 NT imu v10-mpu6000.brd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]
2015-08-13 release nt imu mini 9250 & breakout modules
    [STorM32 NT breakout v10.brd, STorM32 NT breakout v10.sch, STorM32 NT imu v10 mini-mpu9250.brd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]
2015-08-19 release nt motor v11, deprecate nt motor v10 & imu v10 mpu6000
    [STorM32 NT imu module v008 mini.GBL, STorM32 NT imu module v008 mini.GBO, STorM32 NT imu module v008 mini.GBP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]
2016-03-18 release imu modules v11
    [STorM32 NT imu mini v11 imu v11 logger v10 splitter v10 panelized.GBL, STorM32 NT imu mini v11 imu v11 logger v10 splitter v10 panelized.GBO, STorM32 NT imu mi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]
2017-01-12 release v2.x hardware
    [STorM32 NT BGC v242-oshp.brd, STorM32 NT BGC v242.brd, STorM32 NT BGC v242.sch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]
2017-03-09 release TSTorM32 motor modules v24E
    [STorM32 NT BGC v242-molex.brd, STorM32 NT BGC v242-molex.sch, T STorM32 motor v24E-molex.brd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]
2017-05-20 main board v2.4 deprecated
    [STorM32 NT BGC v242-molex.brd, STorM32 NT BGC v242-molex.sch, STorM32 NT BGC v242-oshp.brd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]
2017-07-30 release firmware 2.30
    [storm32web.cfg]
2017-08-03 rerelease v2.30
    [storm32web.cfg]
2017-11-11 release board v3.3, motor v2.5E, oled, esp
    [STorM32 NT BGC v330m.brd, STorM32 NT BGC v330m.sch, STorM32 NT Display v12.brd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]
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2017-12-27 release NT imu v2.11, NT encoder motor v2.51E, display v1.3
    [STorM32 NT Display v13.brd, STorM32 NT Display v13.sch, STorM32 NT imu v211 mini-mpu9250.BOM.csv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]
2018-02-04 release nt logger v1.2
    [STorM32 NT BGC v330m.brd, STorM32 NT BGC v330m.sch, STorM32 NT imu v21 mini-mpu9250-oshp.brd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]
2018-02-22 release NT Logger v1.3
    [STorM32 NT logger v13.brd, STorM32 NT logger v13.sch]
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2018-09-10 T-STorM32 group buy stuff uploaded
    [STorM32 NT BGC v332m sz2u.BOM.xls, STorM32 NT BGC v332m sz2u.brd, STorM32 NT BGC v332m sz2u.sch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]
2019-11-24 storm32 micro release: bgc v3.33i, motor v2.52E, usbpower v0.20
    [STorM32 Micro BGC v333i micro.BOM.csv, STorM32 Micro BGC v333i micro.brd, STorM32 Micro BGC v333i micro.sch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]
2020-05-23 release STorM32 main board v3.33i
    [STorM32 NT BGC v330m.brd, STorM32 NT BGC v330m.sch, STorM32 NT BGC v332m sz2u.BOM.xls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]
2020-05-24 release STorM32 Mirco Motor Triple Board v0.20
    [STorM32 Micro MotorTripple v02 micro.BOM.csv, STorM32 Micro MotorTripple v02 micro.brd, STorM32 Micro MotorTripple v02 micro.sch]
2020-05-28 release STorM32 Micro Motor Triple Board v0.30
    [STorM32 Micro MotorTripple v02 micro.BOM.csv, STorM32 Micro MotorTripple v03 micro.brd, STorM32 Micro MotorTripple v03 micro.sch]
2020-05-28 release STorM32 RPi Hat v0.60, extension board v0.30
    [STorM32 RPiHat Extension v030.brd, STorM32 RPiHat Extension v030.sch, STorM32 RPiHat v060.brd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]
2020-06-05 release STorM32 Micro Logger Board v1.32
    [STorM32 Micro Logger v132 micro.brd, STorM32 Micro Logger v132 micro.sch]
2020-11-17 make folder old, move stuff into it
    [STorM32 NT BGC v332m sz2u.BOM.xls, STorM32 NT BGC v332m sz2u.brd, STorM32 NT BGC v332m sz2u.sch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]
2023-10-29 release STorM32 NT Imu board v4.2 G4
    [STorM32 NT imu v42g4.brd, STorM32 NT imu v42g4.sch]
2024-01-10 release STorM32 NT Logger module v2.2 G4
    [STorM32 NT imu v42g4.brd, STorM32 NT imu v42g4.sch, STorM32 NT logger micro v22g4 000.brd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]
2024-01-19 release STorM32 v4.1 board, design by KrattWorks
    [STorM32 NT Display v13.brd, STorM32 NT Display v13.sch, STorM32 NT ESP8266 module v005.brd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]
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2024-03-27 Gerber files for storm32-nt-imu-v42-g4 and storm32-nt-logger-v2x-g4
    [STorM32 NT imu v42g4_bottom_bom.csv, STorM32 NT imu v42g4_top_bom.csv, STorM32 NT logger micro v22g4 000_bottom_bom.csv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]
2025-05-02 release STorM32 NT Motor module v4.2EC G4
    [T STorM32 NT motor v42ECg4 000.brd, T STorM32 NT motor v42ECg4 000.sch]
2025-05-07 update of STorM32 NT Motor module v4.2EC G4, few corrections&updates (thx to qvertigo)
    [T STorM32 NT motor v42ECg4 001.brd, T STorM32 NT motor v42ECg4 001.sch]

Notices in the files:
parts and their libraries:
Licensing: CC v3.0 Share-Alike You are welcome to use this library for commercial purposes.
